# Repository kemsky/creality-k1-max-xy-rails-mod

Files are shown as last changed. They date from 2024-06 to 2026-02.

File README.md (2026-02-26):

# Creality `K1 Max` XY Rails Mod

## [**!**] There is V2 of this mod: <https://github.com/kemsky/creality-k1-max-xy-rails-mod-v2>

## Description

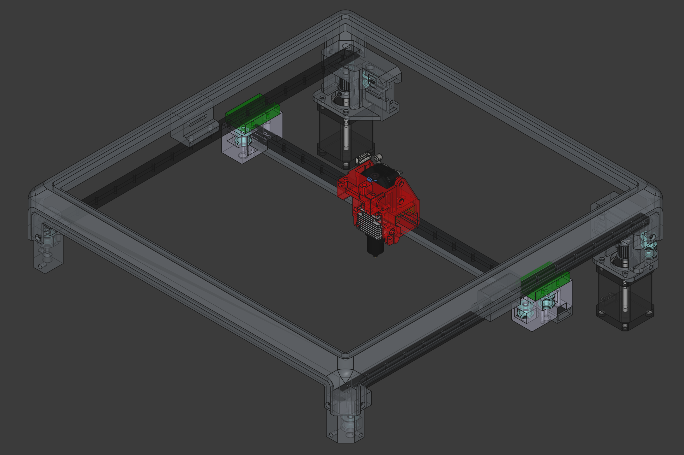
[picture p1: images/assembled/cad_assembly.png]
CAD Assembly


This mod fixes `K1 Max` quality issues, namely excessive ringing/echo. It also increases maximum accelerations.

**You must replace motor pulleys, 7.7mm belt does not fit stock pulleys, alternatively you can install non-stock motors.**

This mod uses `POWGE` 7.7 mm belt and corresponding idler pulleys.
You can use 6 mm belt with stock idlers if you add washers to compensate size differences (`POWGE` idlers have 10.4 mm height, [washers 0.2mm (Affiliate)](https://s.click.aliexpress.com/e/_Dn3ZZa3), [washers 0.3mm (Affiliate)](https://s.click.aliexpress.com/e/_DEptgHN)).

I replaced stock motor pulleys with 20T pulleys for 15mm belt (`rotation_distance` needs to be adjusted to `40` and `driver_SGTHRS` must be tuned `printer.cfg`). You will need a bearing puller to do that (some people use printed pullers e.g. [pulley puller](https://www.printables.com/model/515503-pulley-puller)), you have to be careful to avoid damage to motor shafts. If pulleys sit too tight you can use Dremel and make cuts to relax pulleys.

**You must use camera mount from this mod, it is lower than original.**

**This mod changes print area depending on options you select, beware.**

If you choose motor mounts option 2 - print area should remain the same.

This mod uses `MGN12` rails and `MGN12H` carriages for X and Y axis. All rails must be cut to have 375 mm between far left and far right holes, X axis rail has max length 410 mm (375 + 17.5x2 mm), Y axis rails - 385 mm (375 + 5x2 mm).

Recommended printing materials: PA/PA-CF or similar, ABS-GF. Wall loops, top/bottom layers should be at least 5, I'd recommend 6-7, infill 40%.

### Belts tuning

Preferred way is to use Spectroid Android app (or any other program that can show sound frequency).

Move toolhead to the middle, move X axis to have 150mm between motor mounts and XY joints.

Pluck the shortest belt on each side, displayed frequency should be the same. Target frequency is 120-130Hz, if you go higher than 130Hz you risk to damage belts.

## Published

<https://www.printables.com/model/913734-creality-k1-max-xy-rails-mod>

<https://makerworld.com/en/models/498602>

<https://www.thingiverse.com/thing:6667004>

## License

All work in this repository falls under the Attribution-NonCommercial-ShareAlike 4.0 International (CC BY-NC-SA 4.0).

<https://creativecommons.org/licenses/by-nc-sa/4.0/>

### Notes

Partially this work is based on [D3vil-Design](https://github.com/D3vil-Design/K1-Hardware-Mods) and [Henlor](https://www.printables.com/@Henlor) designs.

## Photos

<details>
    <summary>Front view</summary>
    Front view
</details>

<details>
    <summary>Top view</summary>
    Top view
</details>

<details>
    <summary>Motor mounts</summary>
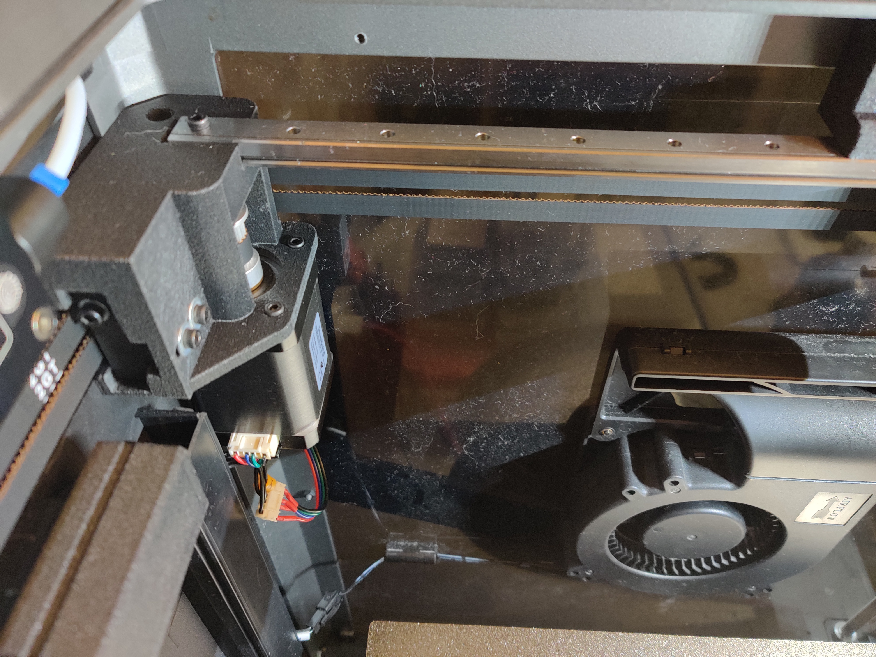
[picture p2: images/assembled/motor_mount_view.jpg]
Motor mounts
    
</details>

<details>
    <summary>Joints</summary>
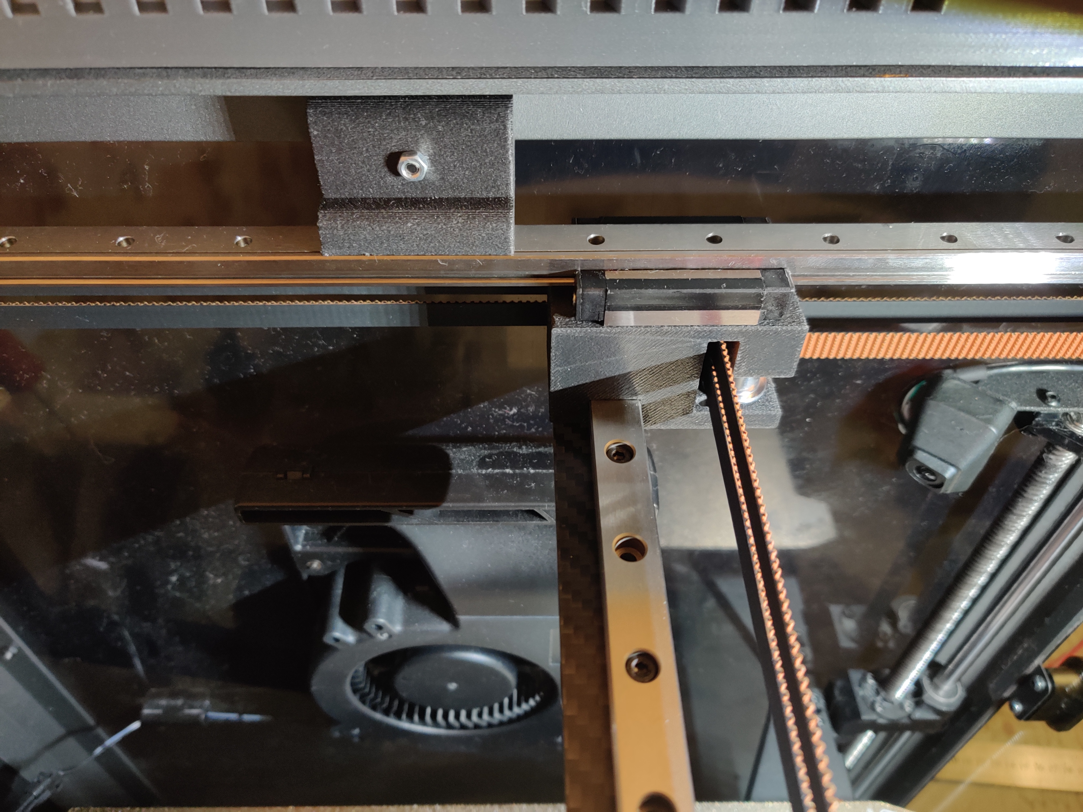
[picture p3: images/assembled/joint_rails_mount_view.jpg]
Joints
    
</details>

<details>
    <summary>Front idlers</summary>
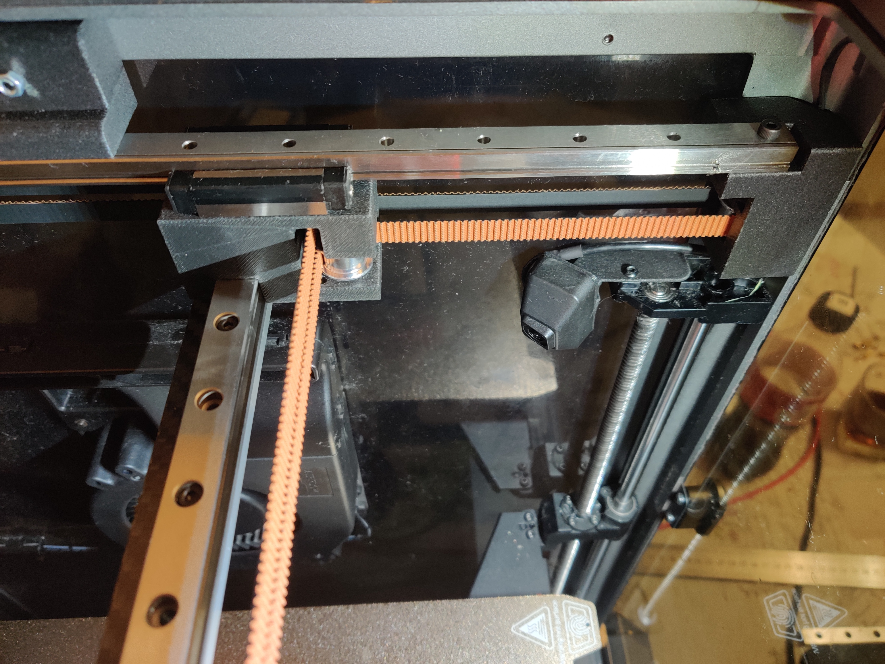
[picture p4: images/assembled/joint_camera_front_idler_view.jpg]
Front idlers
    
</details>

<details>
    <summary>Toolhead</summary>
    Toolhead
</details>

## Input shaper graphs

Input shaper graphs for reinforced X axis (20x5mm aluminium sheet + 20x5mm carbon sheet).

**N.B. Results for Y axis will be worse (two peaks) when X axis is not reinforced or aluminum pipe 20x10x2 is used.**

<details>
    <summary>X axis</summary>
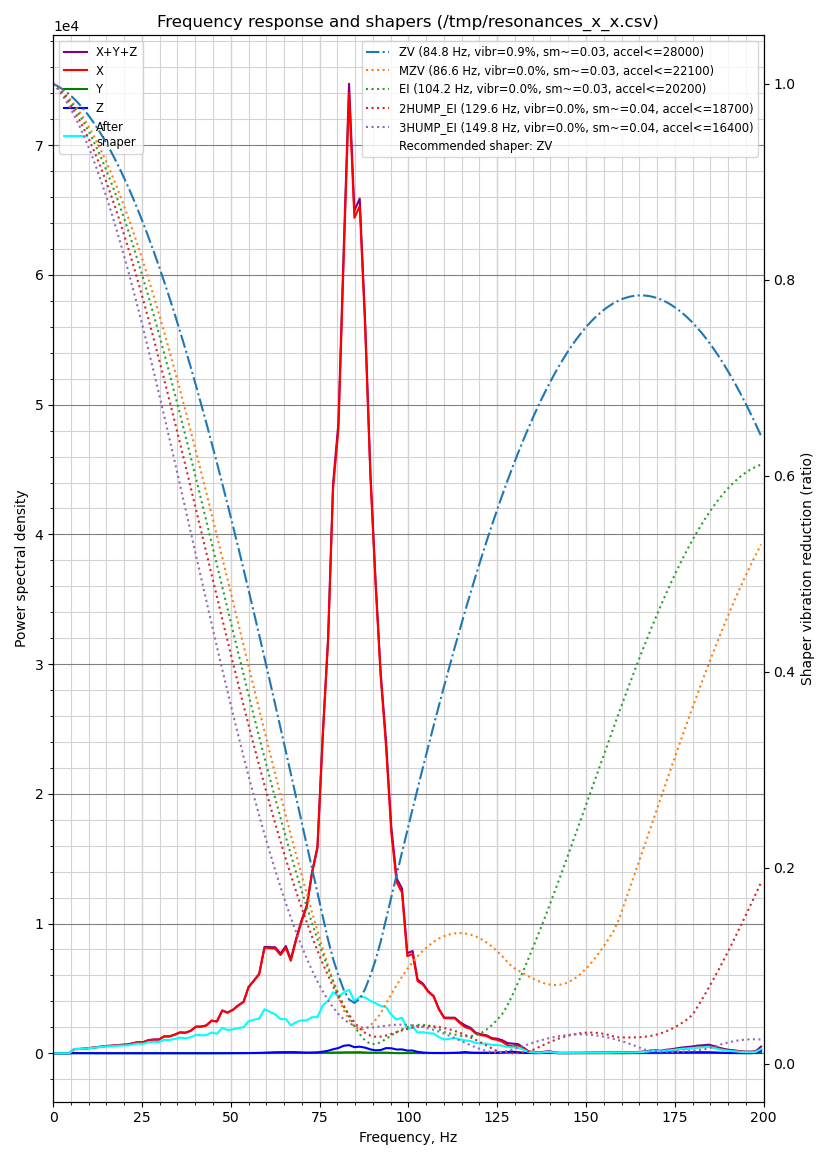
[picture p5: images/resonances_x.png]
X axis
    
</details>

<details>
    <summary>Y axis</summary>
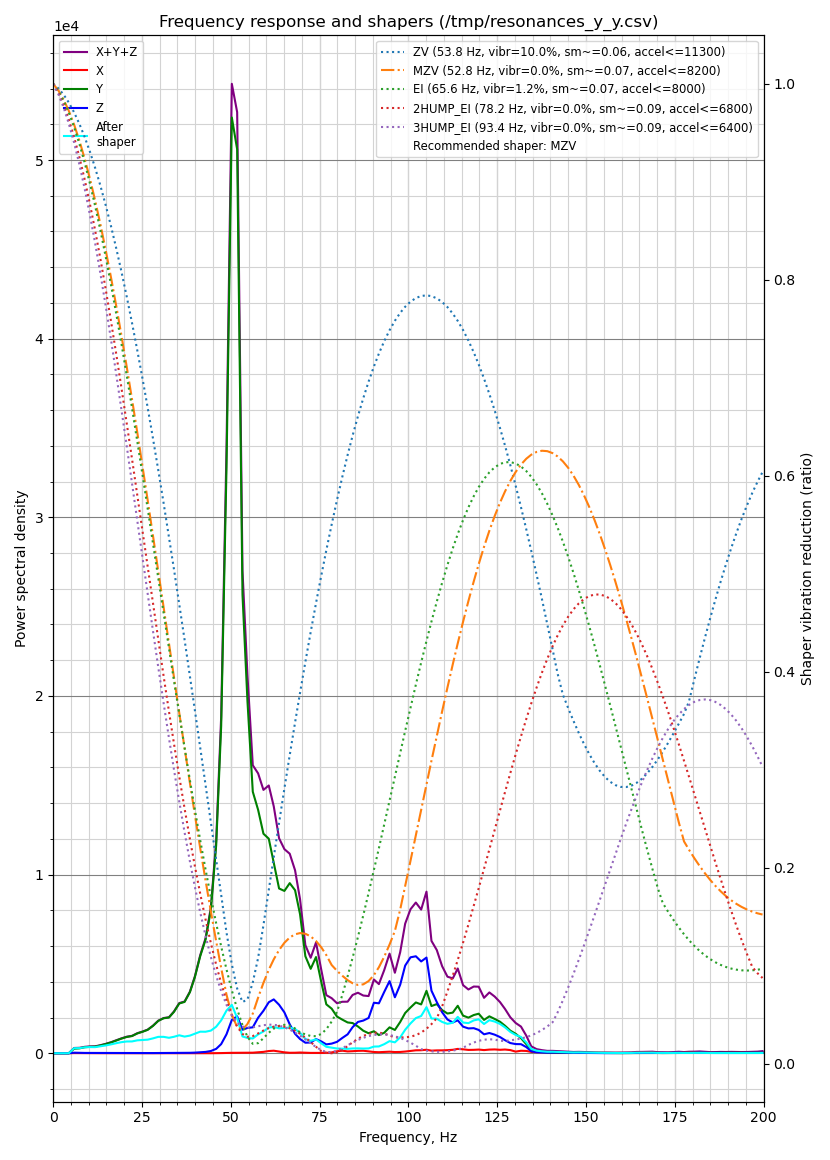
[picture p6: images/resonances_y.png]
Y axis
    
</details>

## VFA

**N.B.** I use 0.9 degree stepper motors - [17HS6401S 0.9 (Affiliate)](https://s.click.aliexpress.com/e/_DeegBeL), they are not ideal, loud, hot and have lower torque than original, but I get less VFA.

Upd. I would recommend Leadshine 42cm06 1.8 motors (low VFA, silent, high torque, need custom wiring, expensive) or LDO-42STH48-1684MAC 0.9 (requires full_steps_per_rotation: 400, loud, limited acceleration, low VFA).

<details>
    <summary>42cm06 1.8 wiring</summary>
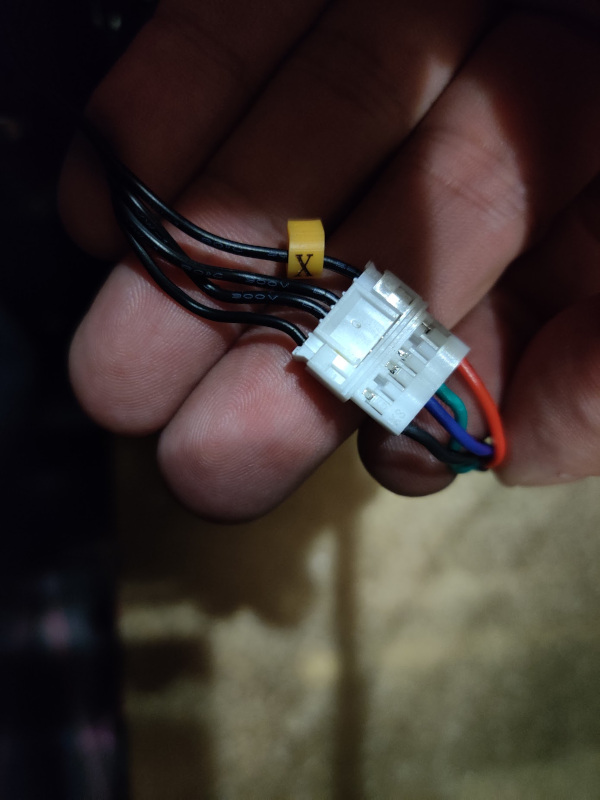
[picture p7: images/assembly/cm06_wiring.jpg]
    
</details>
<br>

<details>
    <summary>eSun Silk PLA</summary>
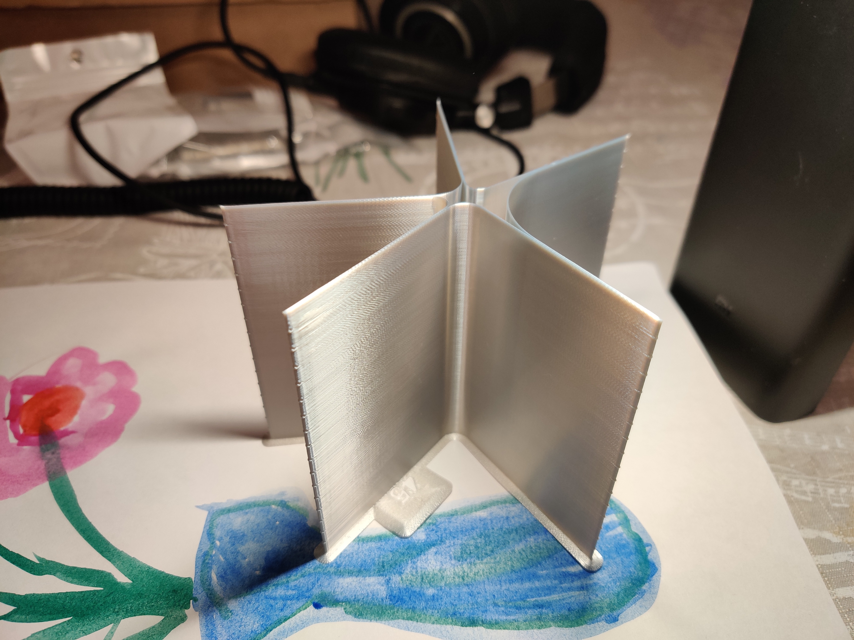
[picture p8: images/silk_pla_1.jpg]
Silk PLA 1
    
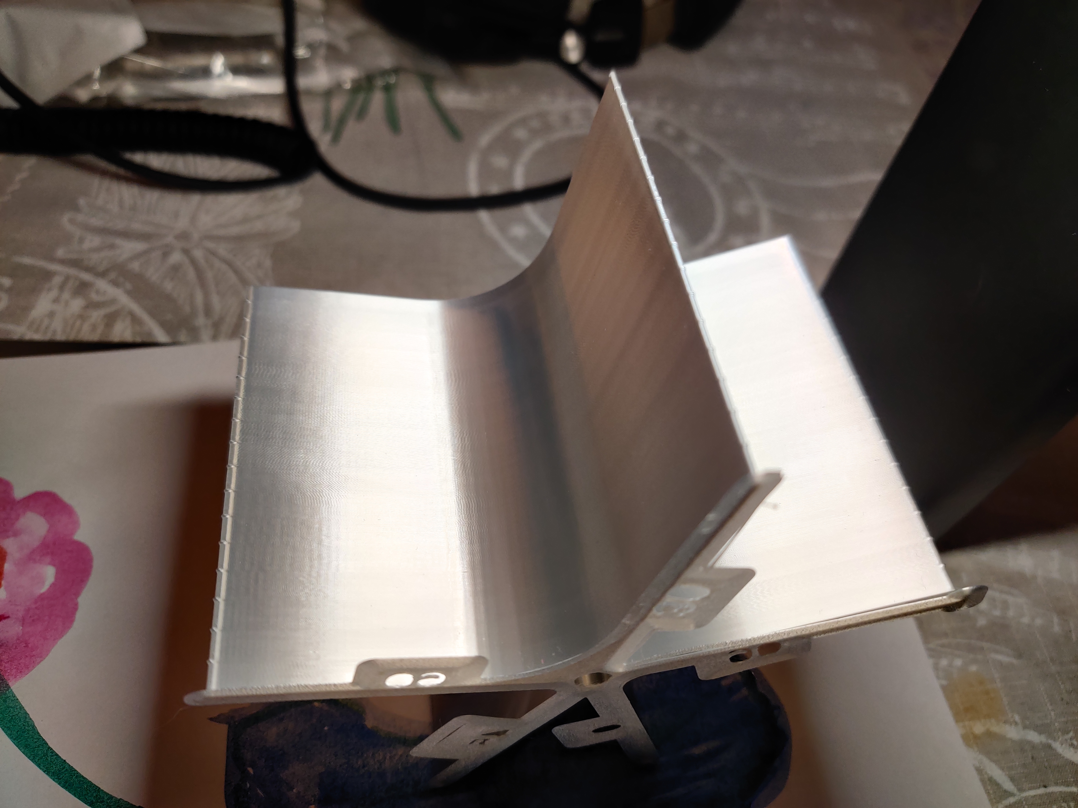
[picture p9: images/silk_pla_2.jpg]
Silk PLA 2
    
</details>

<details>
    <summary>eSun Mate PLA</summary>
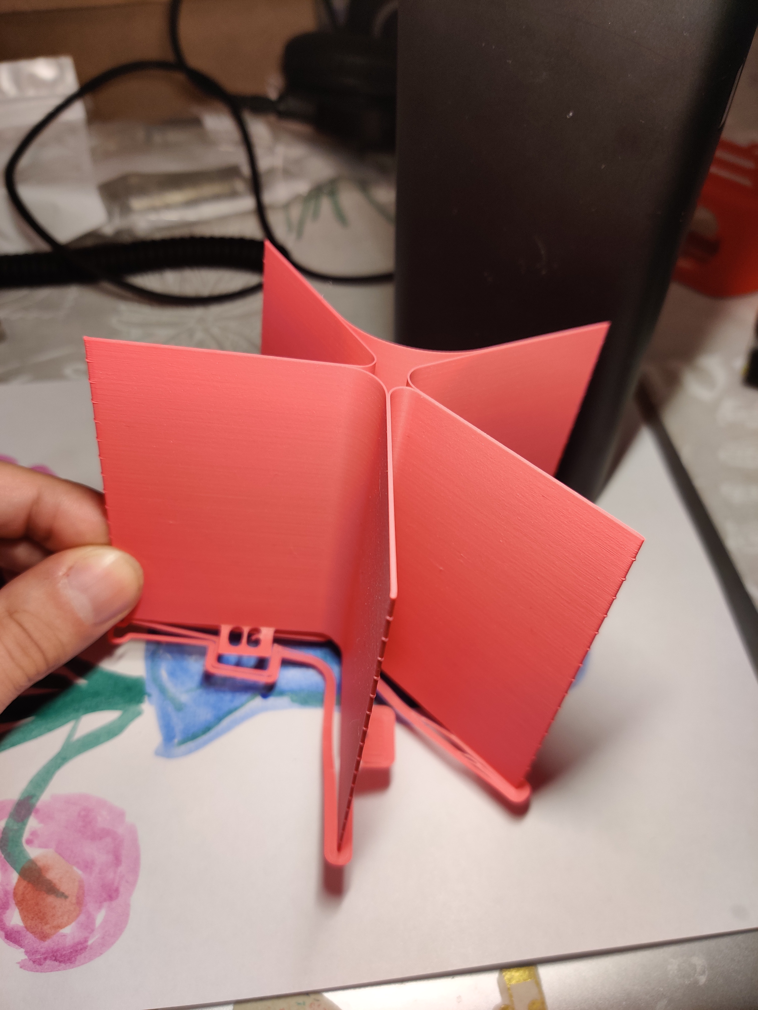
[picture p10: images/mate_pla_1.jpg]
Mate PLA 1
    
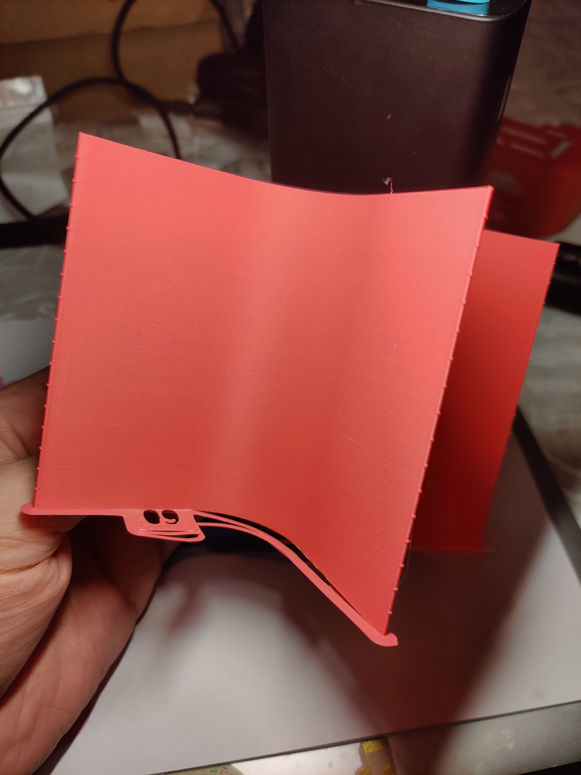
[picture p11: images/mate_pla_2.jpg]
Mate PLA 2
    
</details>

## BOM

BOM contains affiliate links, this way you can support my work if you want.

! `Flat Thin Wafer Head Screw` - M3 screws with flat head that has 1 mm thickness. 
You can find those on AliExpress, manufacturer NINDEJIN, search for "Ultra Low Profile Head Screw".

## Front Idlers

<details>
    <summary>Preview</summary>
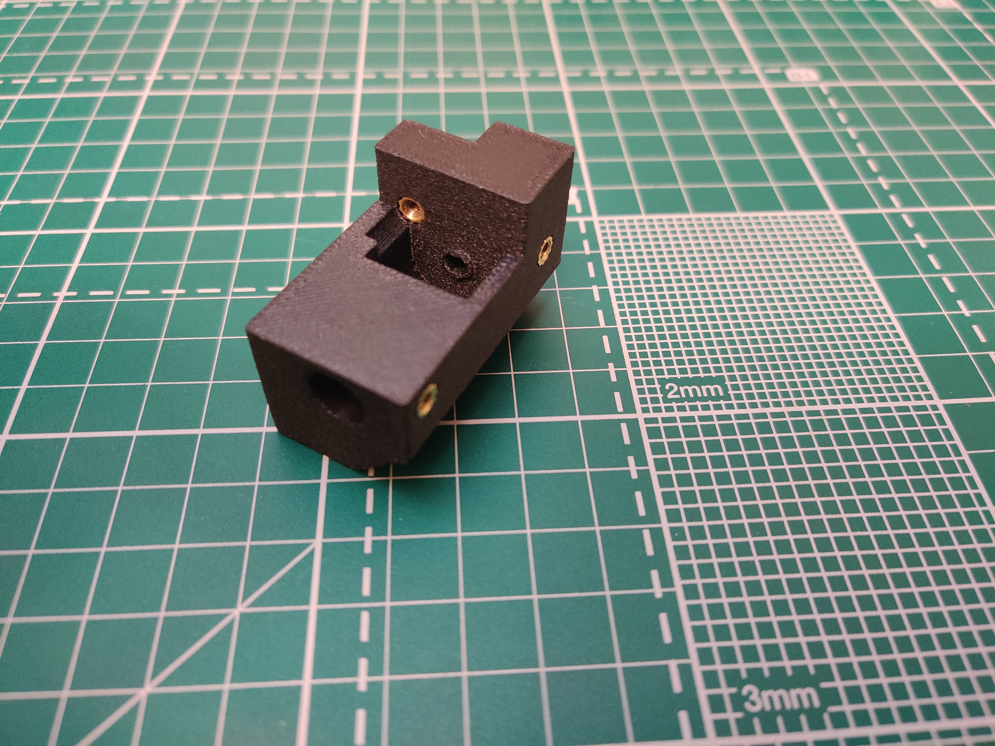
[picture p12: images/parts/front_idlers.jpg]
    
</details>

### Left

[k1_front_idler_left.stl](/stl/k1_front_idler_left.stl)

| Item | Type | Count | Link |
|---|---|---|---|
| DIN 7991 Flat Head Cap Screw | M4 30 mm  | 1 | [AliExpress](https://s.click.aliexpress.com/e/_DkdOkeJ) |
| DIN 7991 Flat Head Cap Screw | M3 6 mm | 4 | [AliExpress](https://s.click.aliexpress.com/e/_DmfmqJh) |
| DIN 912 Socket Head Cap Screw | M3 16 mm  | 1 | [AliExpress](https://s.click.aliexpress.com/e/_DDrYqiJ) |
| POWGE GT2 No Teeth Idler Pulley | 7.7 mm | 1 | [AliExpress](https://s.click.aliexpress.com/e/_DeapZjH) |
| Heat insert | M3 5x5 mm | 5 | [AliExpress](https://s.click.aliexpress.com/e/_DeBGks7) |

### Right

[k1_front_idler_right.stl](/stl/k1_front_idler_right.stl)

| Item | Type | Count | Link |
|---|---|---|---|
| DIN 7991 Flat Head Cap Screw | M4 30 mm  | 1 | [AliExpress](https://s.click.aliexpress.com/e/_DkdOkeJ) |
| DIN 7991 Flat Head Cap Screw | M3 6 mm | 4 | [AliExpress](https://s.click.aliexpress.com/e/_DmfmqJh) |
| DIN 912 Socket Head Cap Screw | M3 16 mm  | 1 | [AliExpress](https://s.click.aliexpress.com/e/_DDrYqiJ) |
| POWGE GT2 No Teeth Idler Pulley | 7.7 mm | 1 | [AliExpress](https://s.click.aliexpress.com/e/_DeapZjH) |
| Heat insert | M3 5x5 mm | 5 | [AliExpress](https://s.click.aliexpress.com/e/_DeBGks7) |

## Camera

[k1_camera.stl](/stl/k1_camera.stl)

## Joints

<details>
    <summary>Preview</summary>
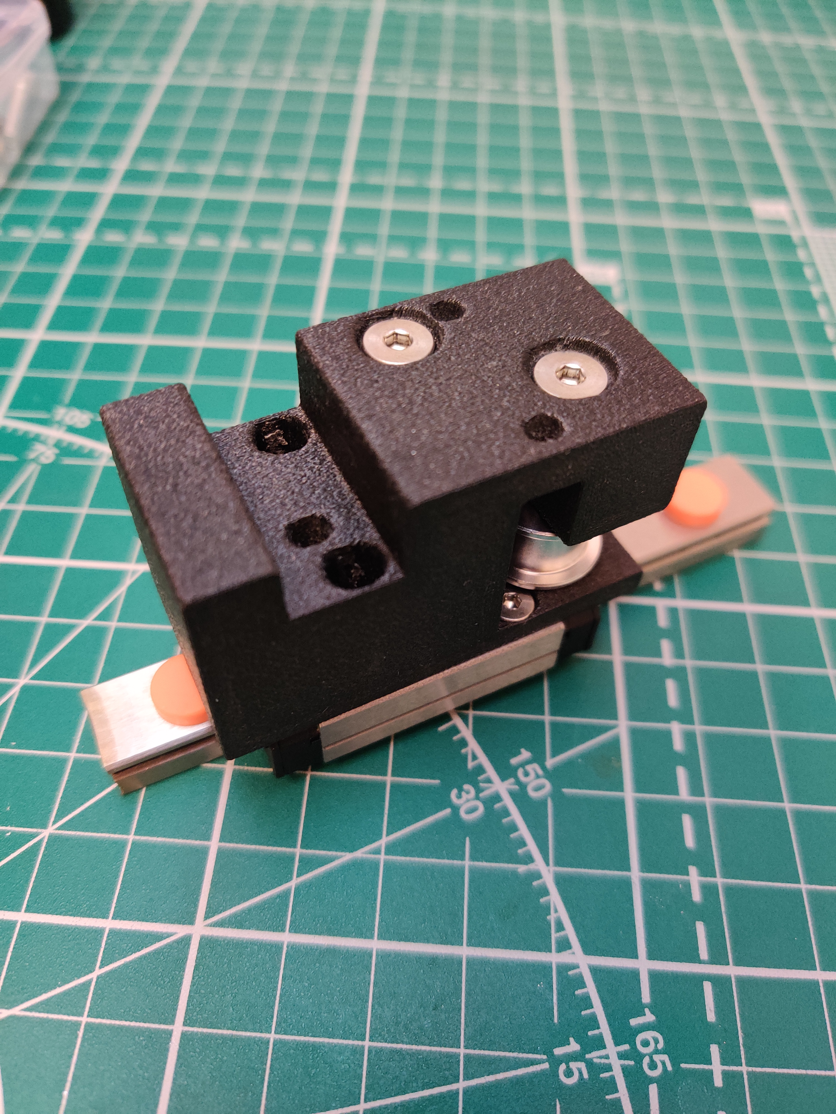
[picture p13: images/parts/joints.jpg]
joints
    
</details>

### Left

[k1_joint_left.stl](/stl/k1_joint_left.stl)

| Item | Type | Count | Link |
|---|---|---|---|
| DIN 7991 Flat Head Cap Screw | M4 30 mm  | 2 | [AliExpress](https://s.click.aliexpress.com/e/_DkdOkeJ) |
| Flat Thin Wafer Head Screw | M3 6 mm | 1 | [AliExpress](https://s.click.aliexpress.com/e/_DFHDPnH) |
| DIN 912 Socket Head Cap Screw | M3 8 mm | 3 | [AliExpress](https://s.click.aliexpress.com/e/_DDrYqiJ) |
| DIN 912 Socket Head Cap Screw | M3 25 mm  | 1 | [AliExpress](https://s.click.aliexpress.com/e/_DDrYqiJ) |
| POWGE GT2 No Teeth Idler Pulley | 7.7 mm | 2 | [AliExpress](https://s.click.aliexpress.com/e/_DeapZjH) |
| Heat insert | M3 5x5 mm | 1 | [AliExpress](https://s.click.aliexpress.com/e/_DeBGks7) |

### Right

[k1_joint_right.stl](/stl/k1_joint_right.stl)

| Item | Type | Count | Link |
|---|---|---|---|
| DIN 7991 Flat Head Cap Screw | M4 30 mm  | 2 | [AliExpress](https://s.click.aliexpress.com/e/_DkdOkeJ) |
| Flat Thin Wafer Head Screw | M3 6 mm | 2 | [AliExpress](https://s.click.aliexpress.com/e/_DFHDPnH) |
| DIN 912 Socket Head Cap Screw | M3 8 mm | 2 | [AliExpress](https://s.click.aliexpress.com/e/_DDrYqiJ) |
| DIN 912 Socket Head Cap Screw | M3 25 mm  | 1 | [AliExpress](https://s.click.aliexpress.com/e/_DDrYqiJ) |
| POWGE GT2 No Teeth Idler Pulley | 7.7 mm | 2 | [AliExpress](https://s.click.aliexpress.com/e/_DeapZjH) |
| Heat insert | M3 5x5 mm | 1 | [AliExpress](https://s.click.aliexpress.com/e/_DeBGks7) |

## Rails mounts

You'll need at least 2 of these for each side.

<details>
    <summary>Preview</summary>
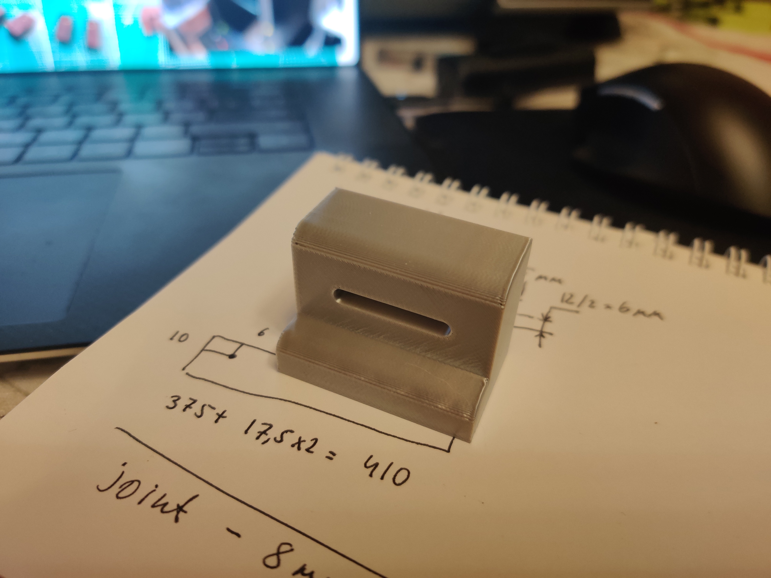
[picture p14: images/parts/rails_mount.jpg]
rails_mount
    
    joint_rails_mount_view
</details>

### Left

[k1_rail_mount.stl](/stl/k1_rail_mount.stl)

| Item | Type | Count | Link |
|---|---|---|---|
| DIN 912 Socket Head Cap Screw | M3 25 mm  | 1 | [AliExpress](https://s.click.aliexpress.com/e/_DDrYqiJ) |
| DIN 912 Socket Head Cap Screw | M3 8 mm | 2 | [AliExpress](https://s.click.aliexpress.com/e/_DDrYqiJ) |
| Heat insert | M3 5x5 mm | 2 | [AliExpress](https://s.click.aliexpress.com/e/_DeBGks7) |

### Right

[k1_rail_mount.stl](/stl/k1_rail_mount.stl)

| Item | Type | Count | Link |
|---|---|---|---|
| DIN 912 Socket Head Cap Screw | M3 25 mm  | 1 | [AliExpress](https://s.click.aliexpress.com/e/_DDrYqiJ) |
| DIN 912 Socket Head Cap Screw | M3 8 mm | 2 | [AliExpress](https://s.click.aliexpress.com/e/_DDrYqiJ) |
| Heat insert | M3 5x5 mm | 2 | [AliExpress](https://s.click.aliexpress.com/e/_DeBGks7) |

## Motor Mounts - Option 1

Use these mounts to simplify build at the cost of reducing print area. The same mounts are used for stock and non-stock motors.

<details>
    <summary>Preview</summary>
    motor_mounts
</details>

### Left

[k1_motor_mount_left.stl](/stl/k1_motor_mount_left.stl)

| Item | Type | Count | Link |
|---|---|---|---|
| DIN 7991 Flat Head Cap Screw | M3 6 mm | 4 | [AliExpress](https://s.click.aliexpress.com/e/_DmfmqJh) |
| DIN 912 Socket Head Cap Screw | M3 6 mm | 2 | [AliExpress](https://s.click.aliexpress.com/e/_DDrYqiJ) |
| DIN 912 Socket Head Cap Screw | M3 16 mm  | 1 | [AliExpress](https://s.click.aliexpress.com/e/_DDrYqiJ) |
| Motor Pulley for 15mm belt | 20T 5 mm  | 1 | [AliExpress](https://s.click.aliexpress.com/e/_opRGeML) |
| POWGE GT2 No Teeth Idler Pulley | 7.7 mm | 2 | [AliExpress](https://s.click.aliexpress.com/e/_DeapZjH) |
| Heat insert | M3 5x5 mm | 6 | [AliExpress](https://s.click.aliexpress.com/e/_DeBGks7) |

You'll need 1 M3x35 screw from stock gantry motor mounts.

### Right

[k1_motor_mount_right.stl](/stl/k1_motor_mount_right.stl)

| Item | Type | Count | Link |
|---|---|---|---|
| DIN 7991 Flat Head Cap Screw | M3 6 mm | 4 | [AliExpress](https://s.click.aliexpress.com/e/_DmfmqJh) |
| DIN 912 Socket Head Cap Screw | M3 6 mm | 2 | [AliExpress](https://s.click.aliexpress.com/e/_DDrYqiJ) |
| DIN 912 Socket Head Cap Screw | M3 16 mm  | 1 | [AliExpress](https://s.click.aliexpress.com/e/_DDrYqiJ) |
| Motor Pulley for 15mm belt | 20T 5 mm  | 1 | [AliExpress](https://s.click.aliexpress.com/e/_opRGeML) |
| POWGE GT2 No Teeth Idler Pulley | 7.7 mm | 2 | [AliExpress](https://s.click.aliexpress.com/e/_DeapZjH) |
| Heat insert | M3 5x5 mm | 6 | [AliExpress](https://s.click.aliexpress.com/e/_DeBGks7) |

You'll need 1 M3x35 screw from stock gantry motor mounts.

## Motor Mounts - Option 2

Use these mounts to preserve print area. Different mounts are used for stock and non-stock motors.

### Motor mount left

<details>
    <summary>Preview</summary>
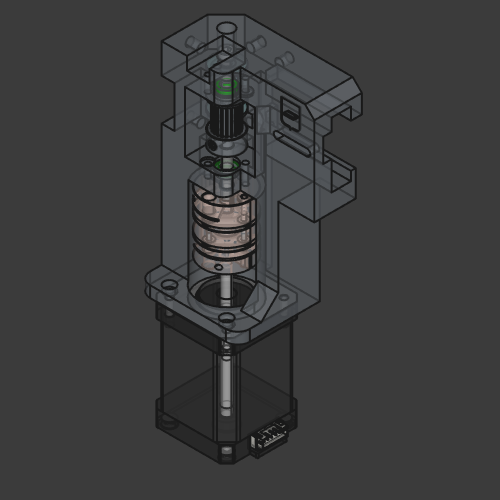
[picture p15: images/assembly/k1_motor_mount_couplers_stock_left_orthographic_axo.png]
k1_motor_mount_couplers_stock_left.stl
    
</details>

- For stock motors - [k1_motor_mount_couplers_stock_left.stl](/stl/k1_motor_mount_couplers_stock_left.stl)
- For non-stock motors - [k1_motor_mount_couplers_left.stl](/stl/k1_motor_mount_couplers_left.stl)

| Item | Type | Count | Link |
|---|---|---|---|
| DIN 7991 Flat Head Cap Screw | M3 6 mm | 4 | [AliExpress](https://s.click.aliexpress.com/e/_DmfmqJh) |
| DIN 912 Socket Head Cap Screw | M3 6 mm | 3 | [AliExpress](https://s.click.aliexpress.com/e/_DDrYqiJ) |
| DIN 912 Socket Head Cap Screw | M3 16 mm  | 1 | [AliExpress](https://s.click.aliexpress.com/e/_DDrYqiJ) |
| Flat Thin Wafer Head Screw | M3 6 mm | 2 | [AliExpress](https://s.click.aliexpress.com/e/_DFHDPnH) |
| MF95ZZ Bearing | | 2 | [AliExpress](https://s.click.aliexpress.com/e/_onsRFx9) |
| Double Diaphragm Coupler | 20x30 5x5 | 1 | [AliExpress](https://s.click.aliexpress.com/e/_opH2rfl) |
| Shaft | 5x57 mm | 1 | [AliExpress](https://s.click.aliexpress.com/e/_oDW10pH) |
| Motor Pulley for 15mm belt | 20T 5 mm  | 1 | [AliExpress](https://s.click.aliexpress.com/e/_opRGeML) |
| POWGE GT2 No Teeth Idler Pulley | 7.7 mm | 2 | [AliExpress](https://s.click.aliexpress.com/e/_DeapZjH) |
| Heat insert | M3 5x5 mm | 5 | [AliExpress](https://s.click.aliexpress.com/e/_DeBGks7) |
| Heat insert | M3 4x5 mm | 1 | [AliExpress](https://s.click.aliexpress.com/e/_DeBGks7) |

You'll need 1 M3x35 screw from stock gantry motor mounts.

### Motor mount right

<details>
    <summary>Preview</summary>
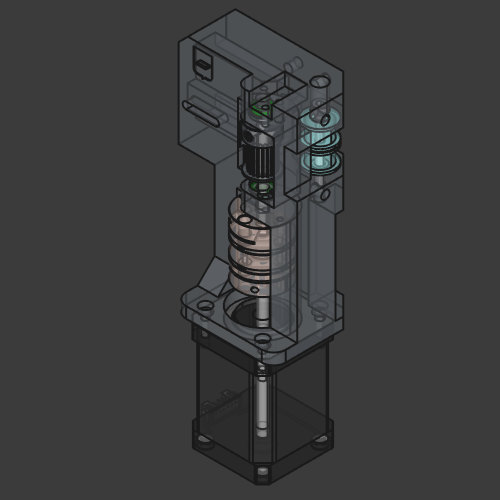
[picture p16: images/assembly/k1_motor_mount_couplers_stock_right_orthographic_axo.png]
k1_motor_mount_couplers_stock_right.stl
    
</details>

- For stock motors - [k1_motor_mount_couplers_stock_right.stl](/stl/k1_motor_mount_couplers_stock_right.stl)
- For non-stock motors - [k1_motor_mount_couplers_right.stl](/stl/k1_motor_mount_couplers_right.stl)

| Item | Type | Count | Link |
|---|---|---|---|
| DIN 7991 Flat Head Cap Screw | M3 6 mm | 4 | [AliExpress](https://s.click.aliexpress.com/e/_DmfmqJh) |
| DIN 912 Socket Head Cap Screw | M3 6 mm | 3 | [AliExpress](https://s.click.aliexpress.com/e/_DDrYqiJ) |
| DIN 912 Socket Head Cap Screw | M3 16 mm  | 1 | [AliExpress](https://s.click.aliexpress.com/e/_DDrYqiJ) |
| Flat Thin Wafer Head Screw | M3 6 mm | 2 | [AliExpress](https://s.click.aliexpress.com/e/_DFHDPnH) |
| MF95ZZ Bearing | | 2 | [AliExpress](https://s.click.aliexpress.com/e/_onsRFx9) |
| Double Diaphragm Coupler | 20x30 5x5 | 1 | [AliExpress](https://s.click.aliexpress.com/e/_opH2rfl) |
| Shaft | 5x57 mm | 1 | [AliExpress](https://s.click.aliexpress.com/e/_oDW10pH) |
| Motor Pulley for 15mm belt | 20T 5 mm  | 1 | [AliExpress](https://s.click.aliexpress.com/e/_opRGeML) |
| POWGE GT2 No Teeth Idler Pulley | 7.7 mm | 2 | [AliExpress](https://s.click.aliexpress.com/e/_DeapZjH) |
| Heat insert | M3 5x5 mm | 5 | [AliExpress](https://s.click.aliexpress.com/e/_DeBGks7) |
| Heat insert | M3 4x5 mm | 1 | [AliExpress](https://s.click.aliexpress.com/e/_DeBGks7) |

You'll need 1 M3x35 screw from stock gantry motor mounts.

## Tensioners

<details>
    <summary>Preview</summary>
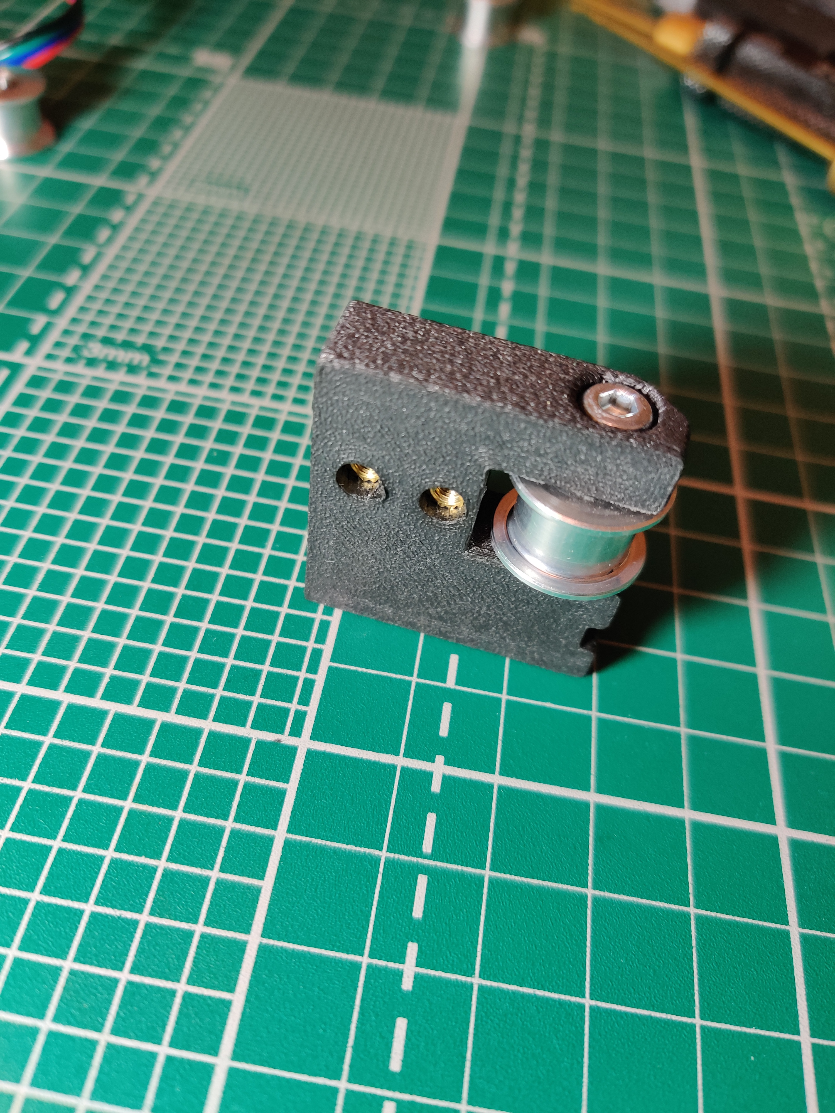
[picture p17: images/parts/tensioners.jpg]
tensioners
    
</details>

### Left

[k1_tensioner_left.stl](/stl/k1_tensioner_left.stl)

| Item | Type | Count | Link |
|---|---|---|---|
| DIN 912 Socket Head Cap Screw | M3 45 mm | 1 | [AliExpress](https://s.click.aliexpress.com/e/_DCYZ5zD) |
| DIN 912 Socket Head Cap Screw | M3 16 mm | 2 | [AliExpress](https://s.click.aliexpress.com/e/_DDrYqiJ) |
| DIN 912 Socket Head Cap Screw | M4 20 mm | 1 | [AliExpress](https://s.click.aliexpress.com/e/_DEOTbEL) |
| POWGE GT2 No Teeth Idler Pulley | 7.7 mm | 1 | [AliExpress](https://s.click.aliexpress.com/e/_DeapZjH) |
| Heat insert | M3 4.5x3 mm | 2 | [AliExpress](https://s.click.aliexpress.com/e/_DeBGks7) |

### Right

[k1_tensioner_right.stl](/stl/k1_tensioner_right.stl)

| Item | Type | Count | Link |
|---|---|---|---|
| DIN 912 Socket Head Cap Screw | M3 45 mm | 1 | [AliExpress](https://s.click.aliexpress.com/e/_DCYZ5zD) |
| DIN 912 Socket Head Cap Screw | M3 16 mm | 2 | [AliExpress](https://s.click.aliexpress.com/e/_DDrYqiJ) |
| DIN 912 Socket Head Cap Screw | M4 20 mm | 1 | [AliExpress](https://s.click.aliexpress.com/e/_DEOTbEL) |
| POWGE GT2 No Teeth Idler Pulley | 7.7 mm | 1 | [AliExpress](https://s.click.aliexpress.com/e/_DeapZjH) |
| Heat insert | M3 4.5x3 mm | 2 | [AliExpress](https://s.click.aliexpress.com/e/_DeBGks7) |

## Toolhead and X axis

There are 2 options for X axis:

1. Rail only - use [k1_toolhead.stl](/stl/k1_toolhead.stl)

   MGN12 rail can be used on X axis without reinforcement, but it is not rigid enough.

   Bed mesh will likely be less accurate, input shaper graph for Y axis will have at least 2 peaks, there will be vibrations on Z axis.

   There is one benefit - you probably will have print area unchanged (both motor mounts options).

2. Rail mounted on 20x10 pipe or 20x5 carbon + 20x5 aluminium sheets - use [k1_toolhead_20x10.stl](/stl/k1_toolhead_20x10.stl)

   Print area will be reduced to 284 mm (Y axis) with motor mounts option 1.

### Aluminium rectangular pipe on X axis

Use rail as drilling template, first make mark using 4 mm drill bit, then drill hole using 2.5 mm drill bit, then tap M3 thread.

<details>
    <summary>Preview</summary>
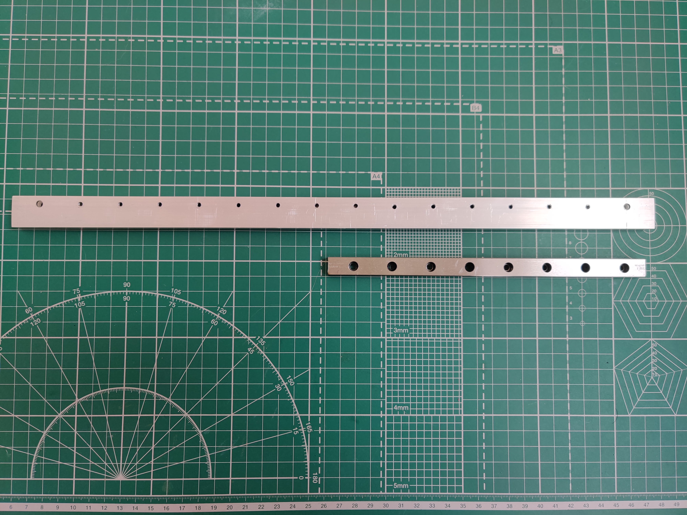
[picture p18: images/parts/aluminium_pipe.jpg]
aluminium_pipe
    
</details>

| Item | Type | Count | Link |
|---|---|---|---|
| Aluminium rectangular pipe | 20x10x2 500 mm | 1 | [AliExpress](https://s.click.aliexpress.com/e/_Defnblp) |
| DIN 912 Socket Head Cap Screw | M3 8 mm | 7-14  | [AliExpress](https://s.click.aliexpress.com/e/_DDrYqiJ) |

### Aluminium and carbon sheet on X axis

Alternatively, you can use 20x5 mm aluminium sheet and 20x5 carbon sheet instead of 20x10 pipe:

<details>
    <summary>Preview</summary>
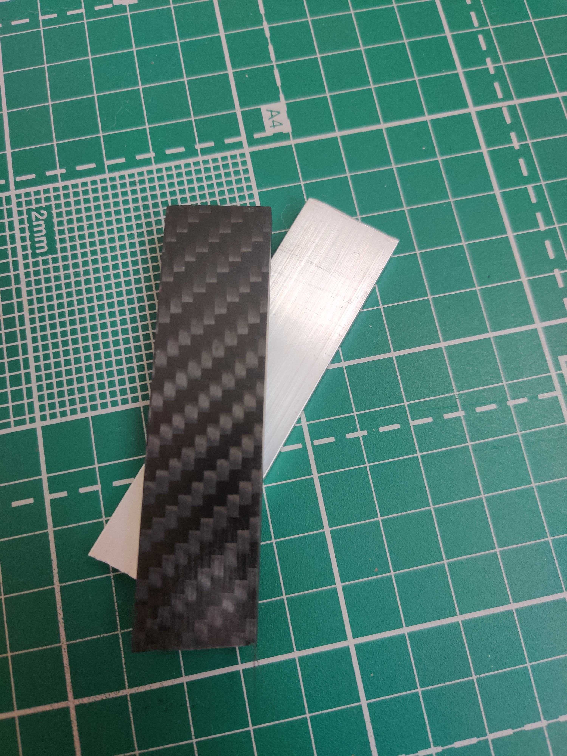
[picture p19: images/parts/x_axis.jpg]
x_axis
    
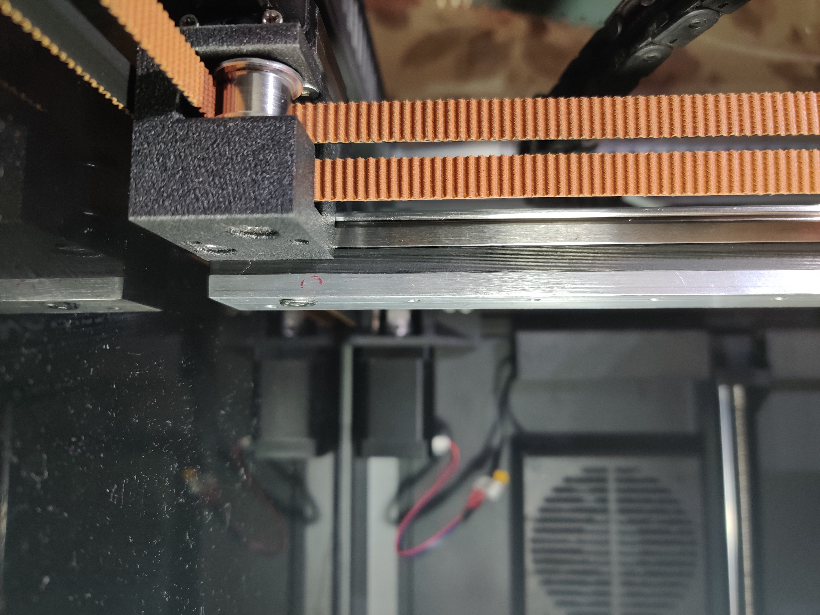
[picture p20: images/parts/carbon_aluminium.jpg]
carbon_aluminium
    
</details>

| Item | Type | Count | Link |
|---|---|---|---|
| Aluminium sheet | 20x5 500 mm | 1 | [AliExpress](https://s.click.aliexpress.com/e/_Dm5qHWj) |
| Carbon fiber sheet | 20x5 500 mm | 1 | [AliExpress](https://s.click.aliexpress.com/e/_DBjpWrt) |
| DIN 912 Socket Head Cap Screw | M3 8 mm | 7-14  | [AliExpress](https://s.click.aliexpress.com/e/_DDrYqiJ) |

### Toolhead

Both toolheads ([k1_toolhead.stl](/stl/k1_toolhead.stl) and [k1_toolhead_20x10.stl](/stl/k1_toolhead_20x10.stl)) use the same set of materials.

<details>
    <summary>Preview</summary>
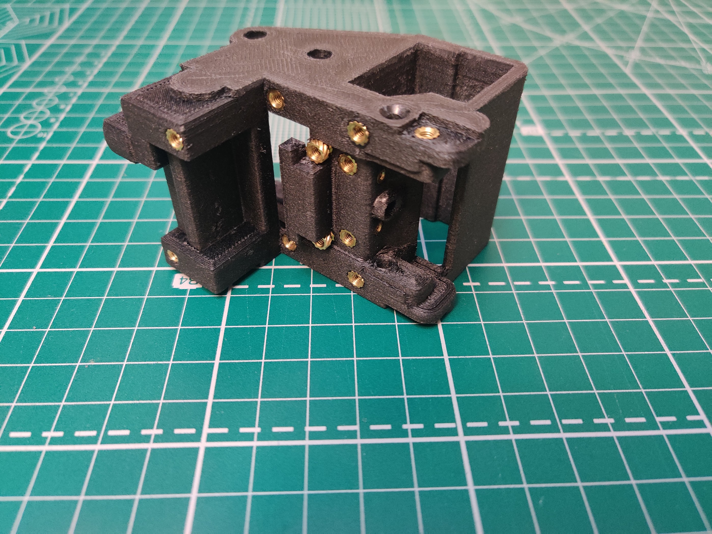
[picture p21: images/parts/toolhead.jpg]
toolhead
    
</details>

| Item | Type | Count | Link |
|---|---|---|---|
| Heat insert | M3 4.5x3 mm | 6 | [AliExpress](https://s.click.aliexpress.com/e/_DeBGks7) |
| Heat insert | M3 5x7 mm | 3 | [AliExpress](https://s.click.aliexpress.com/e/_DeBGks7) |
| Heat insert | M3 5x5 mm | 4 | [AliExpress](https://s.click.aliexpress.com/e/_DeBGks7) |
| Heat insert | M3 5x4 mm | 2 | [AliExpress](https://s.click.aliexpress.com/e/_DeBGks7) |
| Heat insert | M2 3.5x3 mm | 2 | [AliExpress](https://s.click.aliexpress.com/e/_DeBGks7) |

## Other parts

7.7 mm belts increase max accelerations.

| Item | Type | Count | Link |
|---|---|---|---|
| POWGE GT2 belt | 7.7 mm | 1 | [AliExpress](https://s.click.aliexpress.com/e/_DkK1xL9) |
| KGT MGN12H + rail | 400 mm | 2 | [AliExpress](https://s.click.aliexpress.com/e/_DljEcJZ) |
| KGT MGN12H + rail | 500 mm | 1 | [AliExpress](https://s.click.aliexpress.com/e/_DcIqeVl) |

## Tools (optional)

Things you might need, drill bits, taps.

| Item | Type | Count | Link |
|---|---|---|---|
| Hand Tap | 3 mm | 1 | [AliExpress](https://s.click.aliexpress.com/e/_DEEnHLH) |
| Hand Tap Wrench | | 1 | [AliExpress](https://s.click.aliexpress.com/e/_DFq7575) |
| HSS Drill Bits Set  | | 1 | [AliExpress](https://s.click.aliexpress.com/e/_Dmw4uhz) |

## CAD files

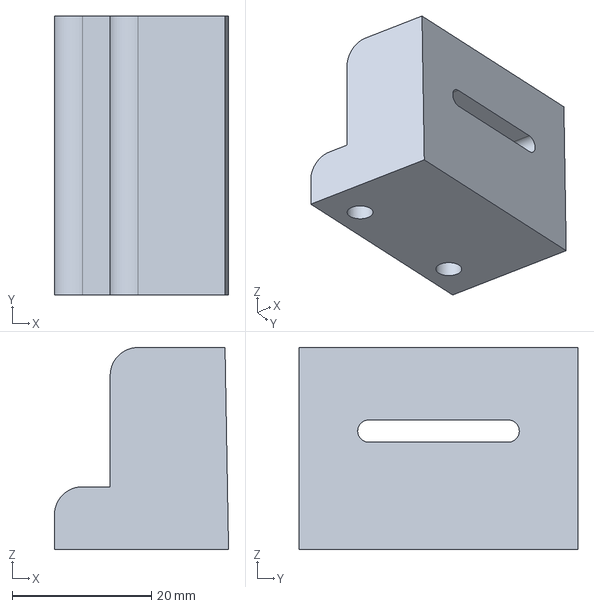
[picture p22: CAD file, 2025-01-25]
src/k1_rail_mount.FCStd
25.0 x 40.0 x 29.0 mm

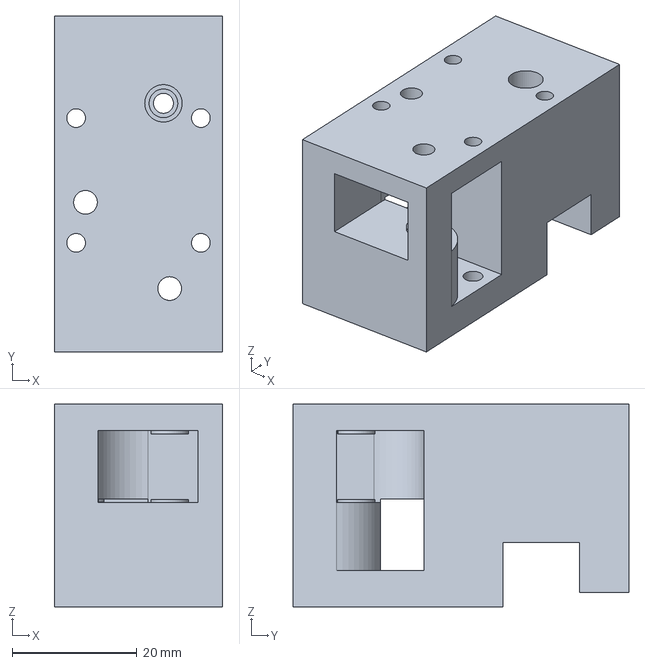
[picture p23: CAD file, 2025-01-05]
src/k1_joint_left.FCStd
27.0 x 53.9 x 32.5 mm

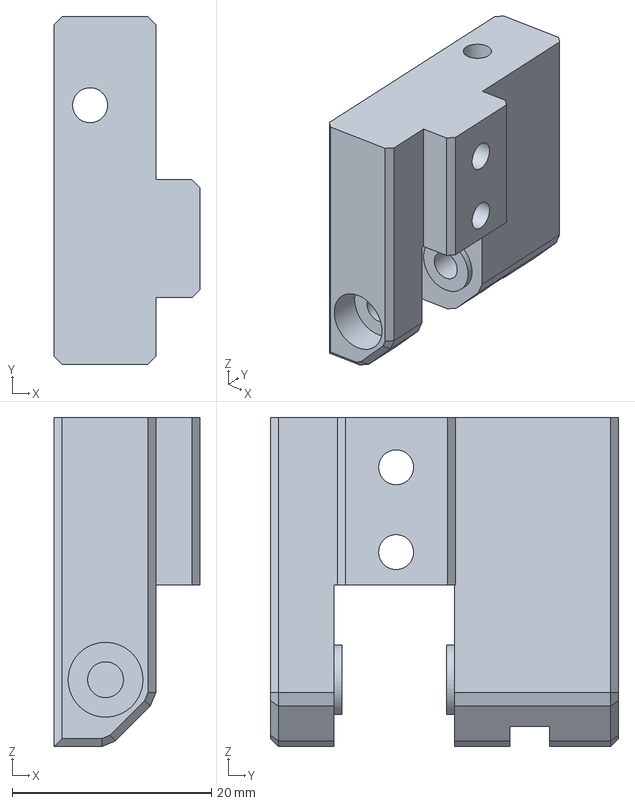
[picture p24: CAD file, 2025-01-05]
step/k1_tensioner_right.step
14.6 x 34.9 x 33.0 mm

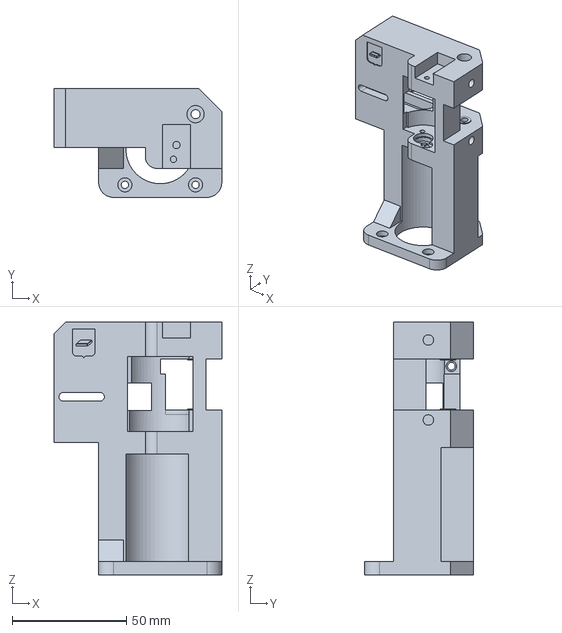
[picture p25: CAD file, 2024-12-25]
step/k1_motor_mount_couplers_stock_right.step
73.5 x 47.7 x 110.9 mm

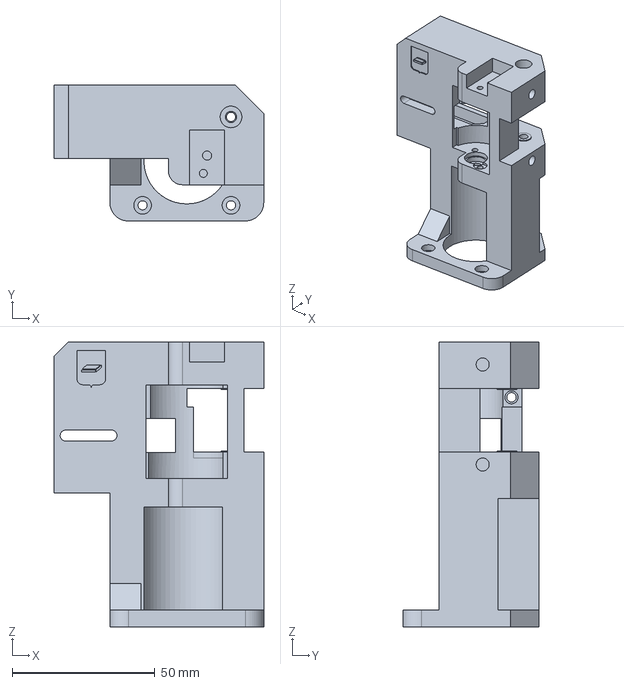
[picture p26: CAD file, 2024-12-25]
step/k1_motor_mount_couplers_right.step
73.5 x 47.7 x 99.9 mm

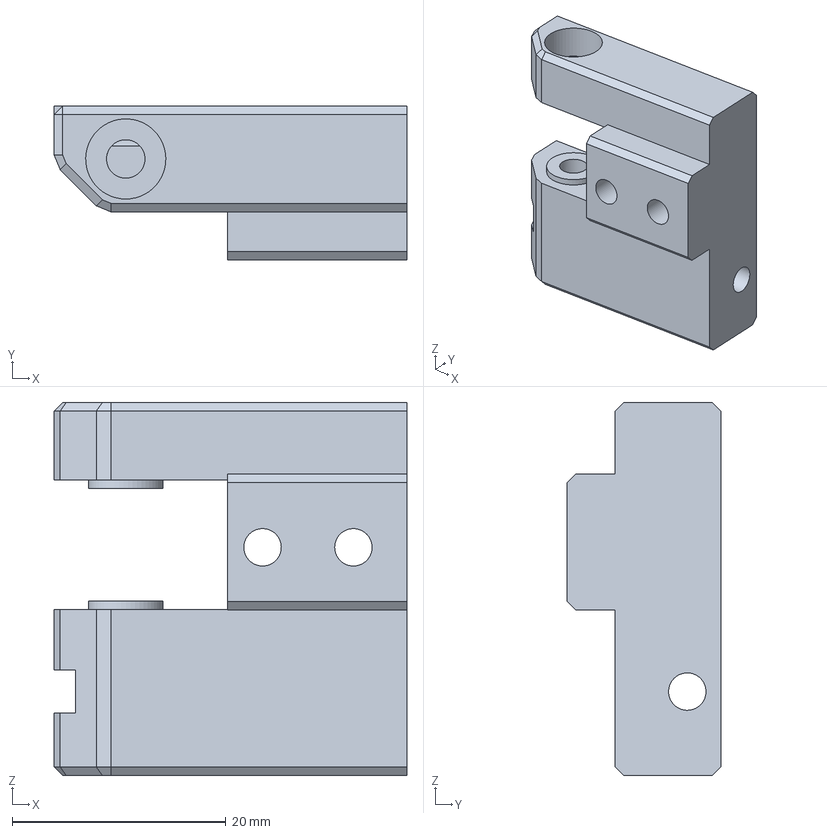
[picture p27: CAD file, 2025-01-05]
src/k1_tensioner_left.FCStd
33.0 x 14.4 x 34.9 mm

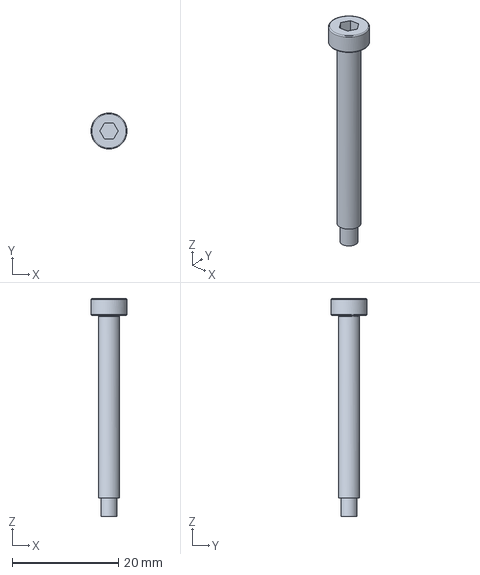
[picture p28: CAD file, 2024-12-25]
src/cad_m4_35mm.FCStd
6.80 x 6.80 x 41.1 mm

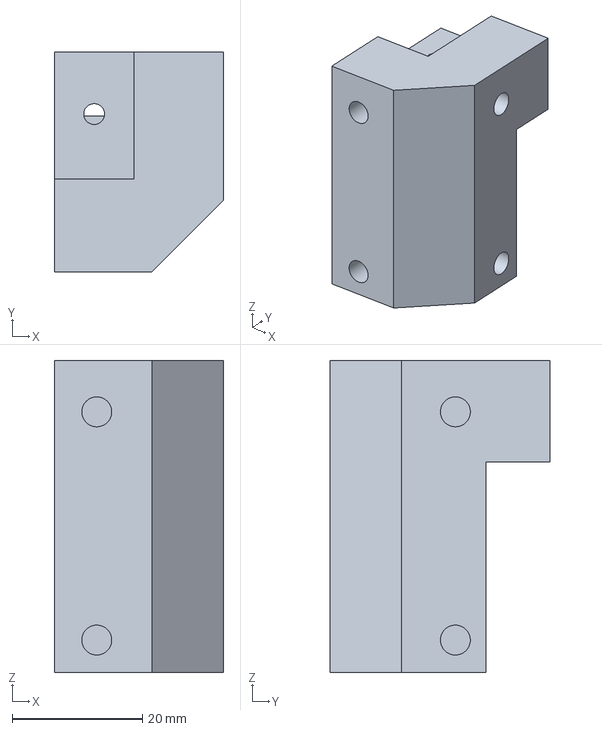
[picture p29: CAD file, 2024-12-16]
step/k1_front_idler_right.step
26.0 x 33.8 x 47.9 mm

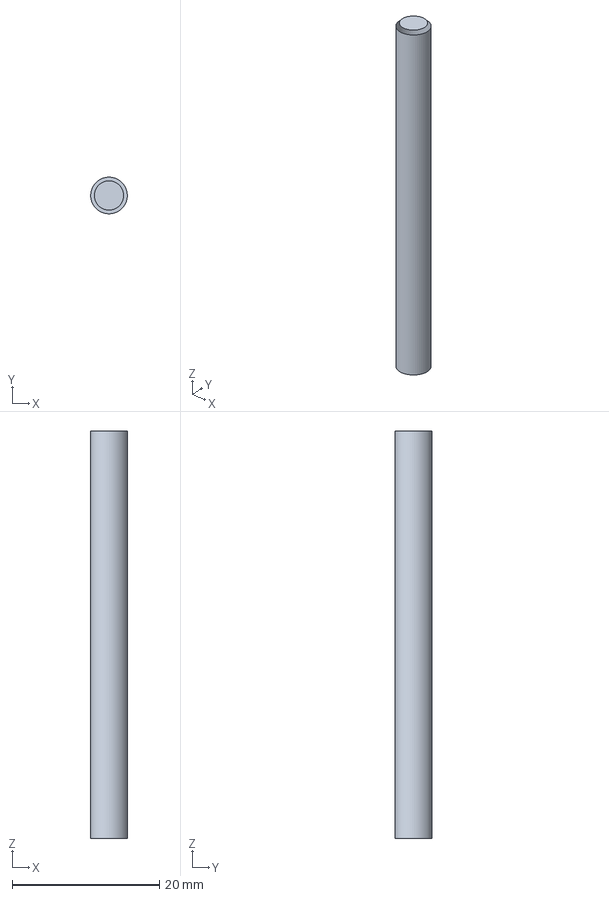
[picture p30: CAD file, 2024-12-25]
src/cad_motor_shaft_55mm.FCStd
4.99 x 4.99 x 55.8 mm

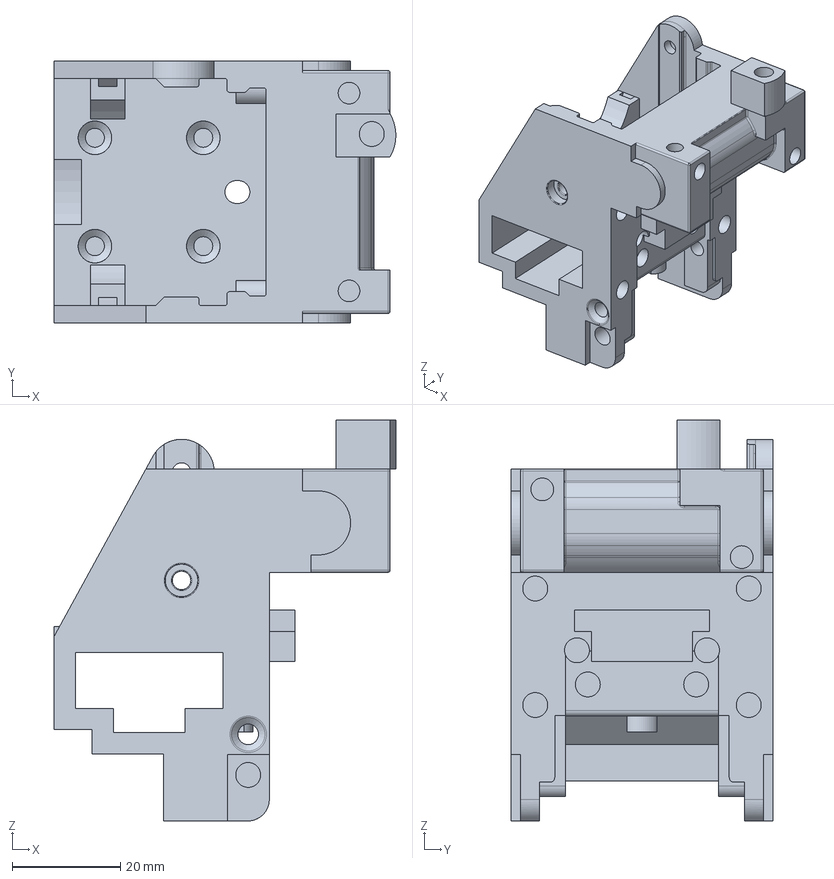
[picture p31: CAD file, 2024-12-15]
step/k1_toolhead.step
63.0 x 48.4 x 74.0 mm

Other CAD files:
src/cad_assembly.FCStd
step/k1_rail_mount.step
src/k1_tensioner_right.FCStd
src/k1_joint_right.FCStd
step/k1_motor_mount_couplers_stock_left.step
src/k1_motor_mount_couplers_right.FCStd
step/k1_motor_mount_couplers_left.step
step/k1_joint_right.step
src/cad_20T_15mm_pulley.FCStd
src/cad_20x10x2.FCStd
src/cad_diaphragm_coupler.FCStd
src/cad_frame_top.FCStd
src/cad_hotend.FCStd
src/cad_mf95zz.FCStd
src/cad_mgn12h_block.FCStd
src/cad_nema17_42_60.FCStd
src/cad_powge_pulley.FCStd
src/cad_rail_mgn12_x.FCStd
src/cad_rail_mgn12_y.FCStd
src/k1_camera.FCStd
src/k1_front_idler_left.FCStd
src/k1_front_idler_right.FCStd
src/k1_motor_mount_couplers_left.FCStd
src/k1_motor_mount_couplers_stock_left.FCStd
src/k1_motor_mount_couplers_stock_right.FCStd
src/k1_motor_mount_left.FCStd
src/k1_motor_mount_right.FCStd
src/k1_toolhead.FCStd
src/k1_toolhead_20x10.FCStd
step/k1_camera.step
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

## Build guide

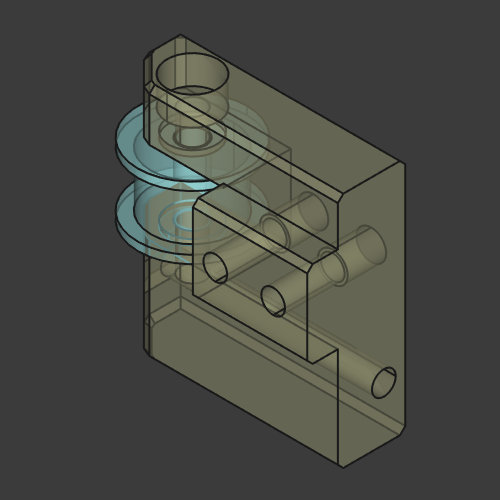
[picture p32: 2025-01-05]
images/assembly/k1_tensioner_left_orthographic_axo.png

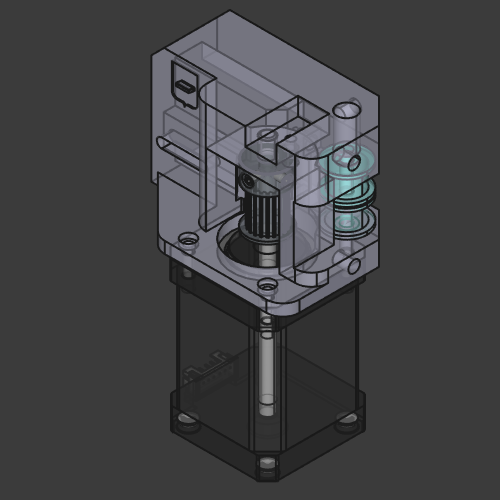
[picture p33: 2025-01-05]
images/assembly/k1_motor_mount_right_orthographic_axo.png

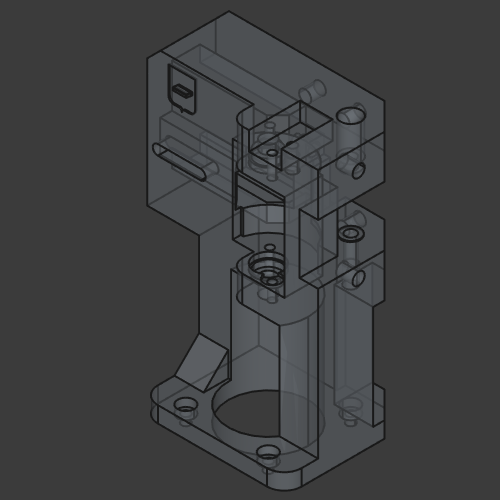
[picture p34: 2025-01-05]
images/assembly/k1_motor_mount_couplers_right_orthographic_axo.png

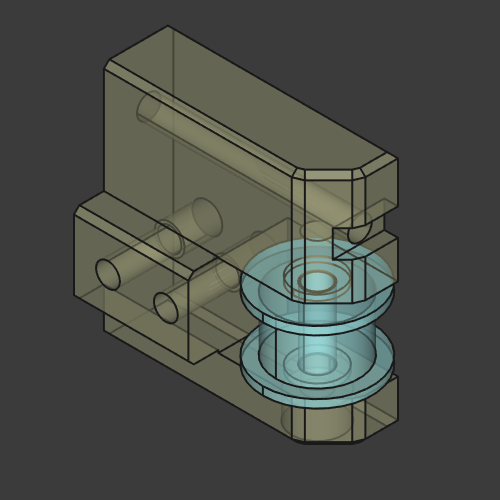
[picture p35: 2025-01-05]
images/assembly/k1_tensioner_right_orthographic_axo.png

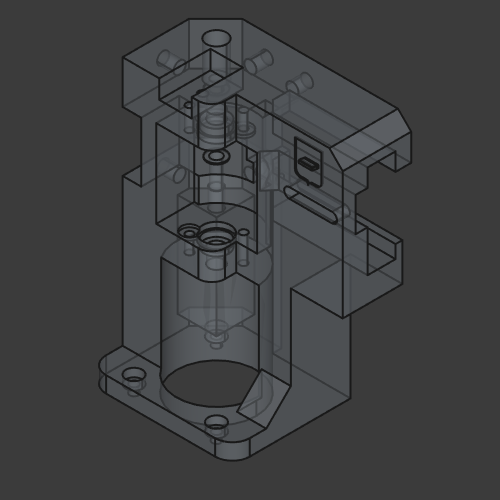
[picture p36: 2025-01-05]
images/assembly/k1_motor_mount_couplers_left_orthographic_axo.png

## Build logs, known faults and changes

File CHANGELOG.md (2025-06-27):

### 2025-06-27

- updated readme

### 2025-01-25

- rails mount wall now has 1 degree angle to fit top frame better

### 2024-12-26

- added motor mounts with couplers to preserve print area

### 2024-12-16

- export automation
- added assembly

### 2024-11-07

- fixed left and right joints, made them more rigid, printer should become less noisy with this fix

### 2024-10-19

- updated readme

### 2024-09-19

- updated toolhead_20x10 to make it lighter and compatible with unicorns

### 2024-09-13

- added toolhead photo and BOM

### 2024-09-05

- fixed left belt tensioner model
- fixed `rail_mount.stl`
- added note about motor pulleys

### 2024-06-16

Initial release

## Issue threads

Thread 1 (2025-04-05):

Mod K1 max

EvdokimovAG84, 2025-04-05:
Добрый день, уважаемый автор мода. Чтобы оставить область печати без изменений, какой из файлов мотора нужно взять? А так же возможно ли быть с Вами на связи в телеграмм, если вдруг возникнут вопросы?

kemsky, 2025-04-05:
@EvdokimovAG84, если нужно сохранить область печати то это [Motor Mount Option 2](https://github.com/kemsky/creality-k1-max-xy-rails-mod?tab=readme-ov-file#motor-mounts---option-2). Недавно на притаблс выложили собранную с фотками: https://www.printables.com/make/2515943.

Лучше пишите вопросы тут.

Closed 2025-04-17.

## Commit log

2024-06-16 update docs
    [belt_tensioner_left.stl, belt_tensioner_right.stl, camera_8mm_lower.stl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]
2024-09-05 update guide, fix model
    [belt_tensioner_left.step, belt_tensioner_left.stl]
2024-09-05 add link to printed puller
2024-09-05 fix rail_mount.stl
    [rail_mount.stl]
2024-09-13 add toolhead
2024-09-19 update toolhead_20x10
    [toolhead_20x10.step, toolhead_20x10.stl]
2024-11-06 update joints
    [joint_left.step, joint_left.stl, joint_right.step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]
2024-12-25 preserve print area
    [cad_assembly.FCStd, cad_diaphragm_coupler.FCStd, cad_m4_35mm.FCStd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]
2025-01-05 update placements and screenshots
    [k1_joint_left.FCStd, k1_joint_right.FCStd, k1_tensioner_left.FCStd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]
2025-01-25 update rail mounts
    [k1_rail_mount.FCStd, k1_rail_mount.step, k1_rail_mount.stl]
2025-06-27 add belts tuning info
